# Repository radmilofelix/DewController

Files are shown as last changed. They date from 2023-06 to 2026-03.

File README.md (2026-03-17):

# DewController
 **Device to control the dew heaters and fans on astronomic instruments**
 
 Dew is an obvious nuisance for astronomic instruments and a simple way of getting rid of it are heaters placed on elements of the optical chain susceptible to forming dew.

The described device is a 6 channel heater driver, and a 2 channel fan driver, as some reflecting telescopes have a fan installed on the back of the main mirror.

The heaters and fans are driven by PWM signals software controlled by means of a STM32F103 microcontroller. The connection with the computer can be achieved either through USB or Ethernet (TCP/IP) or both.
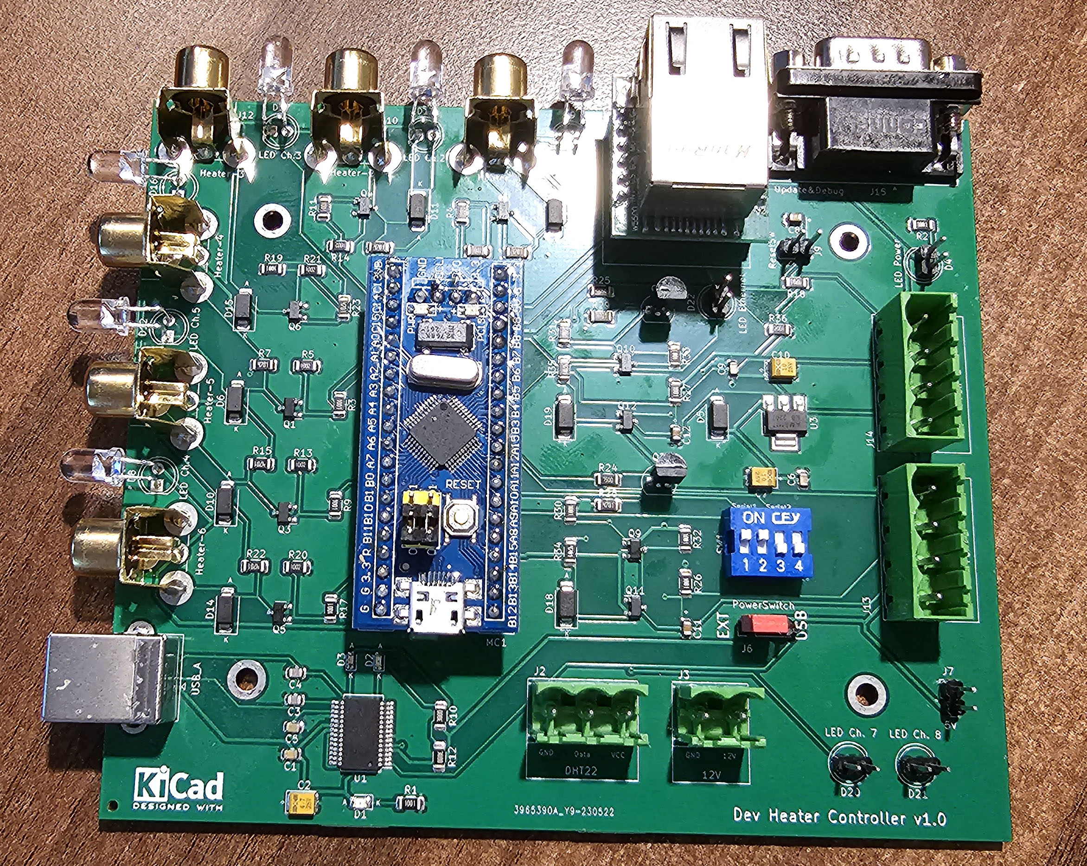
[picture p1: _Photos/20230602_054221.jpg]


The device also has a DHT22 temperature & humidity sensor, so the dew point can be computed to get an indication of whether the heaters have to be powered and how much power has to be supplied to the heaters.

# Description
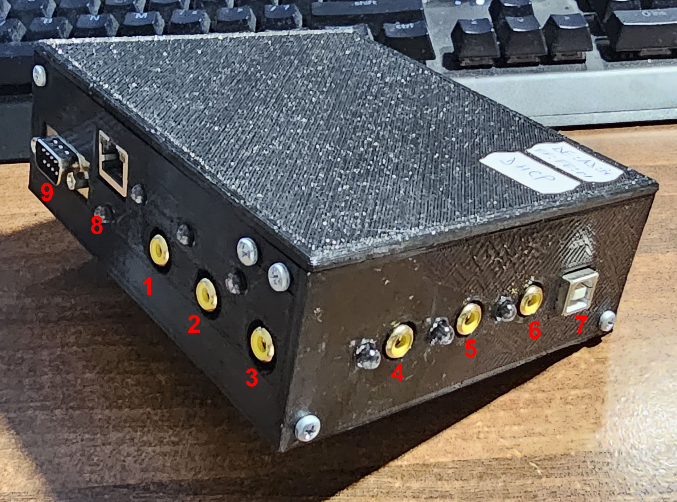
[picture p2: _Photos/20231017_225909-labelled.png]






1.  - Heater 1 (connector and LED)
2.  - Heater 2 (connector and LED)
3.  - Heater 3 (connector and LED)
4.  - Heater 4 (connector and LED)
5.  - Heater 5 (connector and LED)
6.  - Heater 6 (connector and LED)
7.  - USB connector
8.  - Ethernet Connector
9.  - Connector for servicing - 9 pin
10.  - Fan 1 (connector and LED)
11.  - Fan 2 (connector and LED)
12. - DHT 22 sensor
13. - 12V power connector
14. - Reset button
15. - Bracket for mounting the device on the telescope

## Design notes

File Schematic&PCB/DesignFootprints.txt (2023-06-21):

RCA female connectors

D-SUB 9 male connector ????

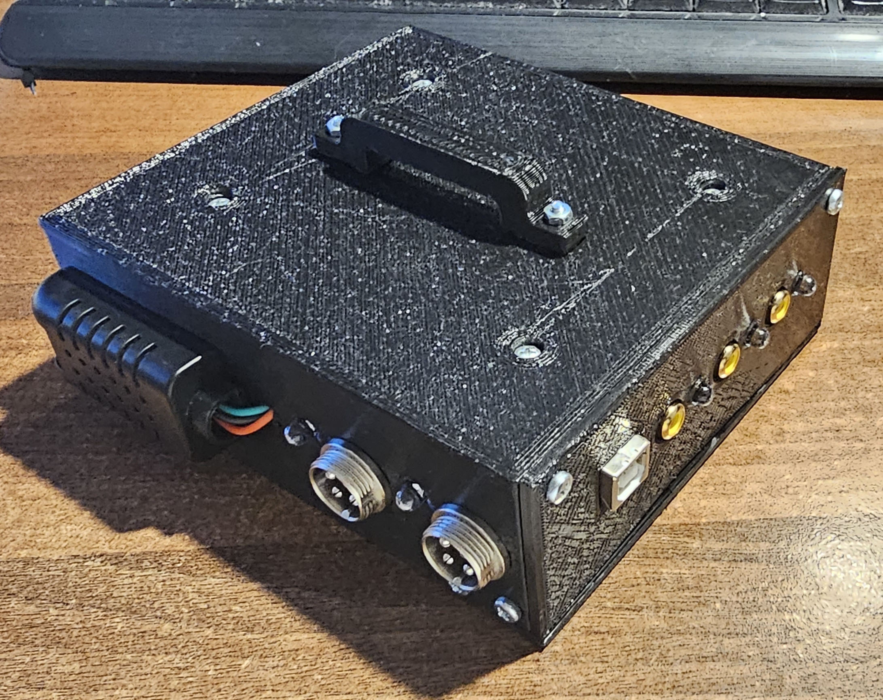
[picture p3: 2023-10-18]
_Photos/20230621_223318-labelled.jpg

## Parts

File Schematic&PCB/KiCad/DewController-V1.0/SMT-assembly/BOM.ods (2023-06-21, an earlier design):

Comment | Designator | Footprint | LCSC
100n | C1, C5, C6, C9 | Capacitor_SMD:C_0805_2012Metric | C49678
4.7u | C2 | Capacitor_Tantalum_SMD:CP_EIA-3528-21_Kemet-B | C1779
47p | C3, C4 | Capacitor_SMD:C_0805_2012Metric | C14857
10u | C7, C10 | Capacitor_Tantalum_SMD:CP_EIA-3528-21_Kemet-B | C140404
1u | C8, C11, C12 | Capacitor_SMD:C_0805_2012Metric | C28323
LED – 0805 | D1 | LED_SMD:LED_1206_3216Metric | C84256
LED Blue | D2 | LED_SMD:LED_0603_1608Metric | C72038
LED Red | D3 | LED_SMD:LED_0603_1608Metric | C72043
1N4007 | D5 | Diode_SMD:D_SMA | C22452
1N4007 | D6, D7, D10, D11, D14, D15, D18, D19 | Diode_SMD:D_SMA | C22452
IRLR3410TRPBF-SOT-23-3L-AO3400A | Q1, Q2, Q3, Q4, Q5, Q6, Q9, Q10 | Package_TO_SOT_SMD:TO-252-2 | C20917
HY19P03D-SOT23-AO3401A | Q11, Q12 | Package_TO_SOT_SMD:TO-252-2 | C15127
1k | R1 | Resistor_SMD:R_1206_3216Metric | C4410
1K | R2, R3, R4, R9, R11, R17, R19, R26, R27, R30, R31, R32, R33 | Resistor_SMD:R_1206_3216Metric | C4410
12K-10k | R5, R6, R13, R14, R20, R21 | Resistor_SMD:R_1206_3216Metric | C17902
6.8K-4.7k | R7, R8, R15, R16, R22, R23, R34, R35 | Resistor_SMD:R_1206_3216Metric | C17936
270-300 | R10, R12 | Resistor_SMD:R_1206_3216Metric | C17887
5k-4.7k | R18 | Resistor_SMD:R_1206_3216Metric | C17936
510-750 | R24, R25 | Resistor_SMD:R_1206_3216Metric | C17985
5K-4.7k | R28, R29 | Resistor_SMD:R_1206_3216Metric | C17936
3K | R36 | Resistor_SMD:R_1206_3216Metric | C17944
FT232RL | U1 | Package_SO:SSOP-28_5.3x10.2mm_P0.65mm | C8690
AZ1117-5.0 – AMS1117-5.0 | U3 | Package_TO_SOT_SMD:SOT-223 | C6187

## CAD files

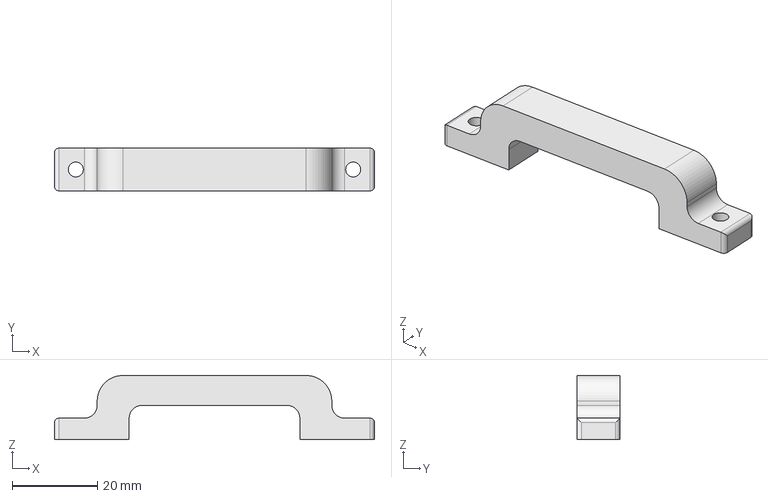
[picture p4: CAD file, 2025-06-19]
MechanicalDesigns/Case/CaseHolder.FCStd
75.0 x 10.0 x 15.0 mm

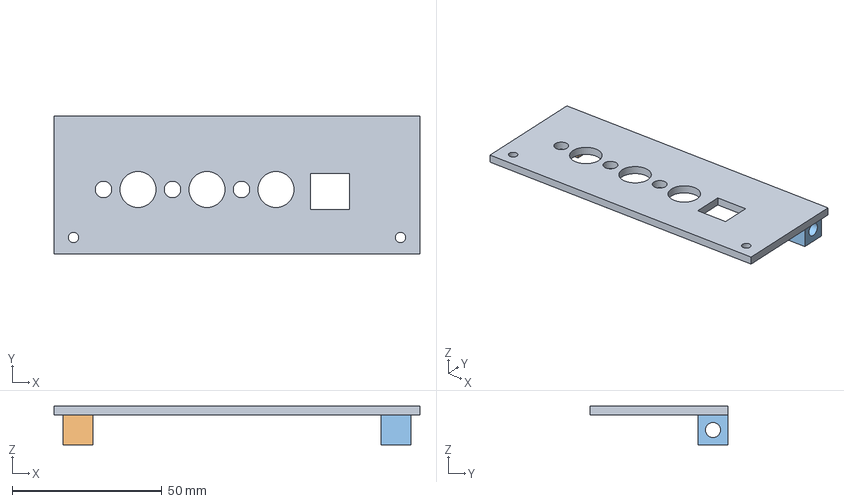
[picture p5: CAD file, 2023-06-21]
MechanicalDesigns/Case/LateralWall.FCStd
122.0 x 46.0 x 13.0 mm
M3x9_001
M3x9_002

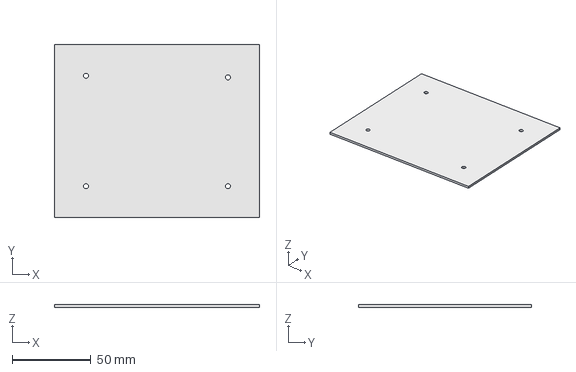
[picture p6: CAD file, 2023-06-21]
MechanicalDesigns/Case/PCB.FCStd
130.0 x 110.0 x 1.60 mm

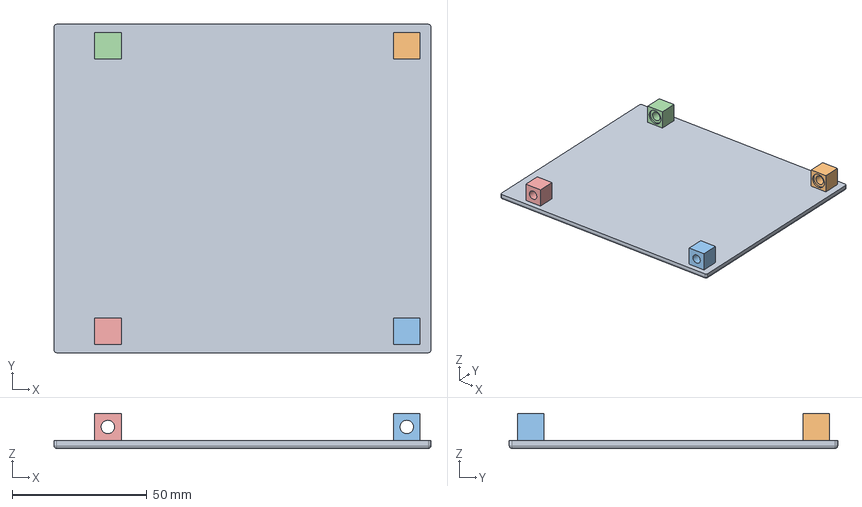
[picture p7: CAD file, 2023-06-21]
MechanicalDesigns/Case/Lid.FCStd
140.0 x 122.0 x 13.0 mm
M3x9_001
M3x9_002
M3x9_003
M3x9_004

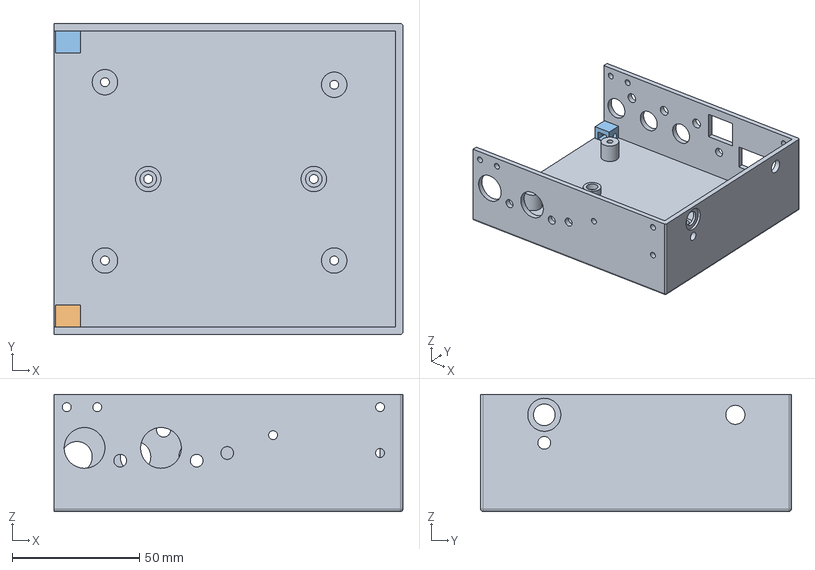
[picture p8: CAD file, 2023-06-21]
MechanicalDesigns/Case/Case.FCStd
137.0 x 122.0 x 46.0 mm
NutHolder-M3x5.7-D4.5-Knurled_Body_001
NutHolder-M3x5.7-D4.5-Knurled_001

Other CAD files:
MechanicalDesigns/Case/CaseHolder-Body.stl
MechanicalDesigns/Case/Case-Old-00.FCStd
MechanicalDesigns/Case/Case-Old-01.FCStd
MechanicalDesigns/Case/Case.stl
MechanicalDesigns/Case/LateralWall.stl
MechanicalDesigns/Case/Lid.stl

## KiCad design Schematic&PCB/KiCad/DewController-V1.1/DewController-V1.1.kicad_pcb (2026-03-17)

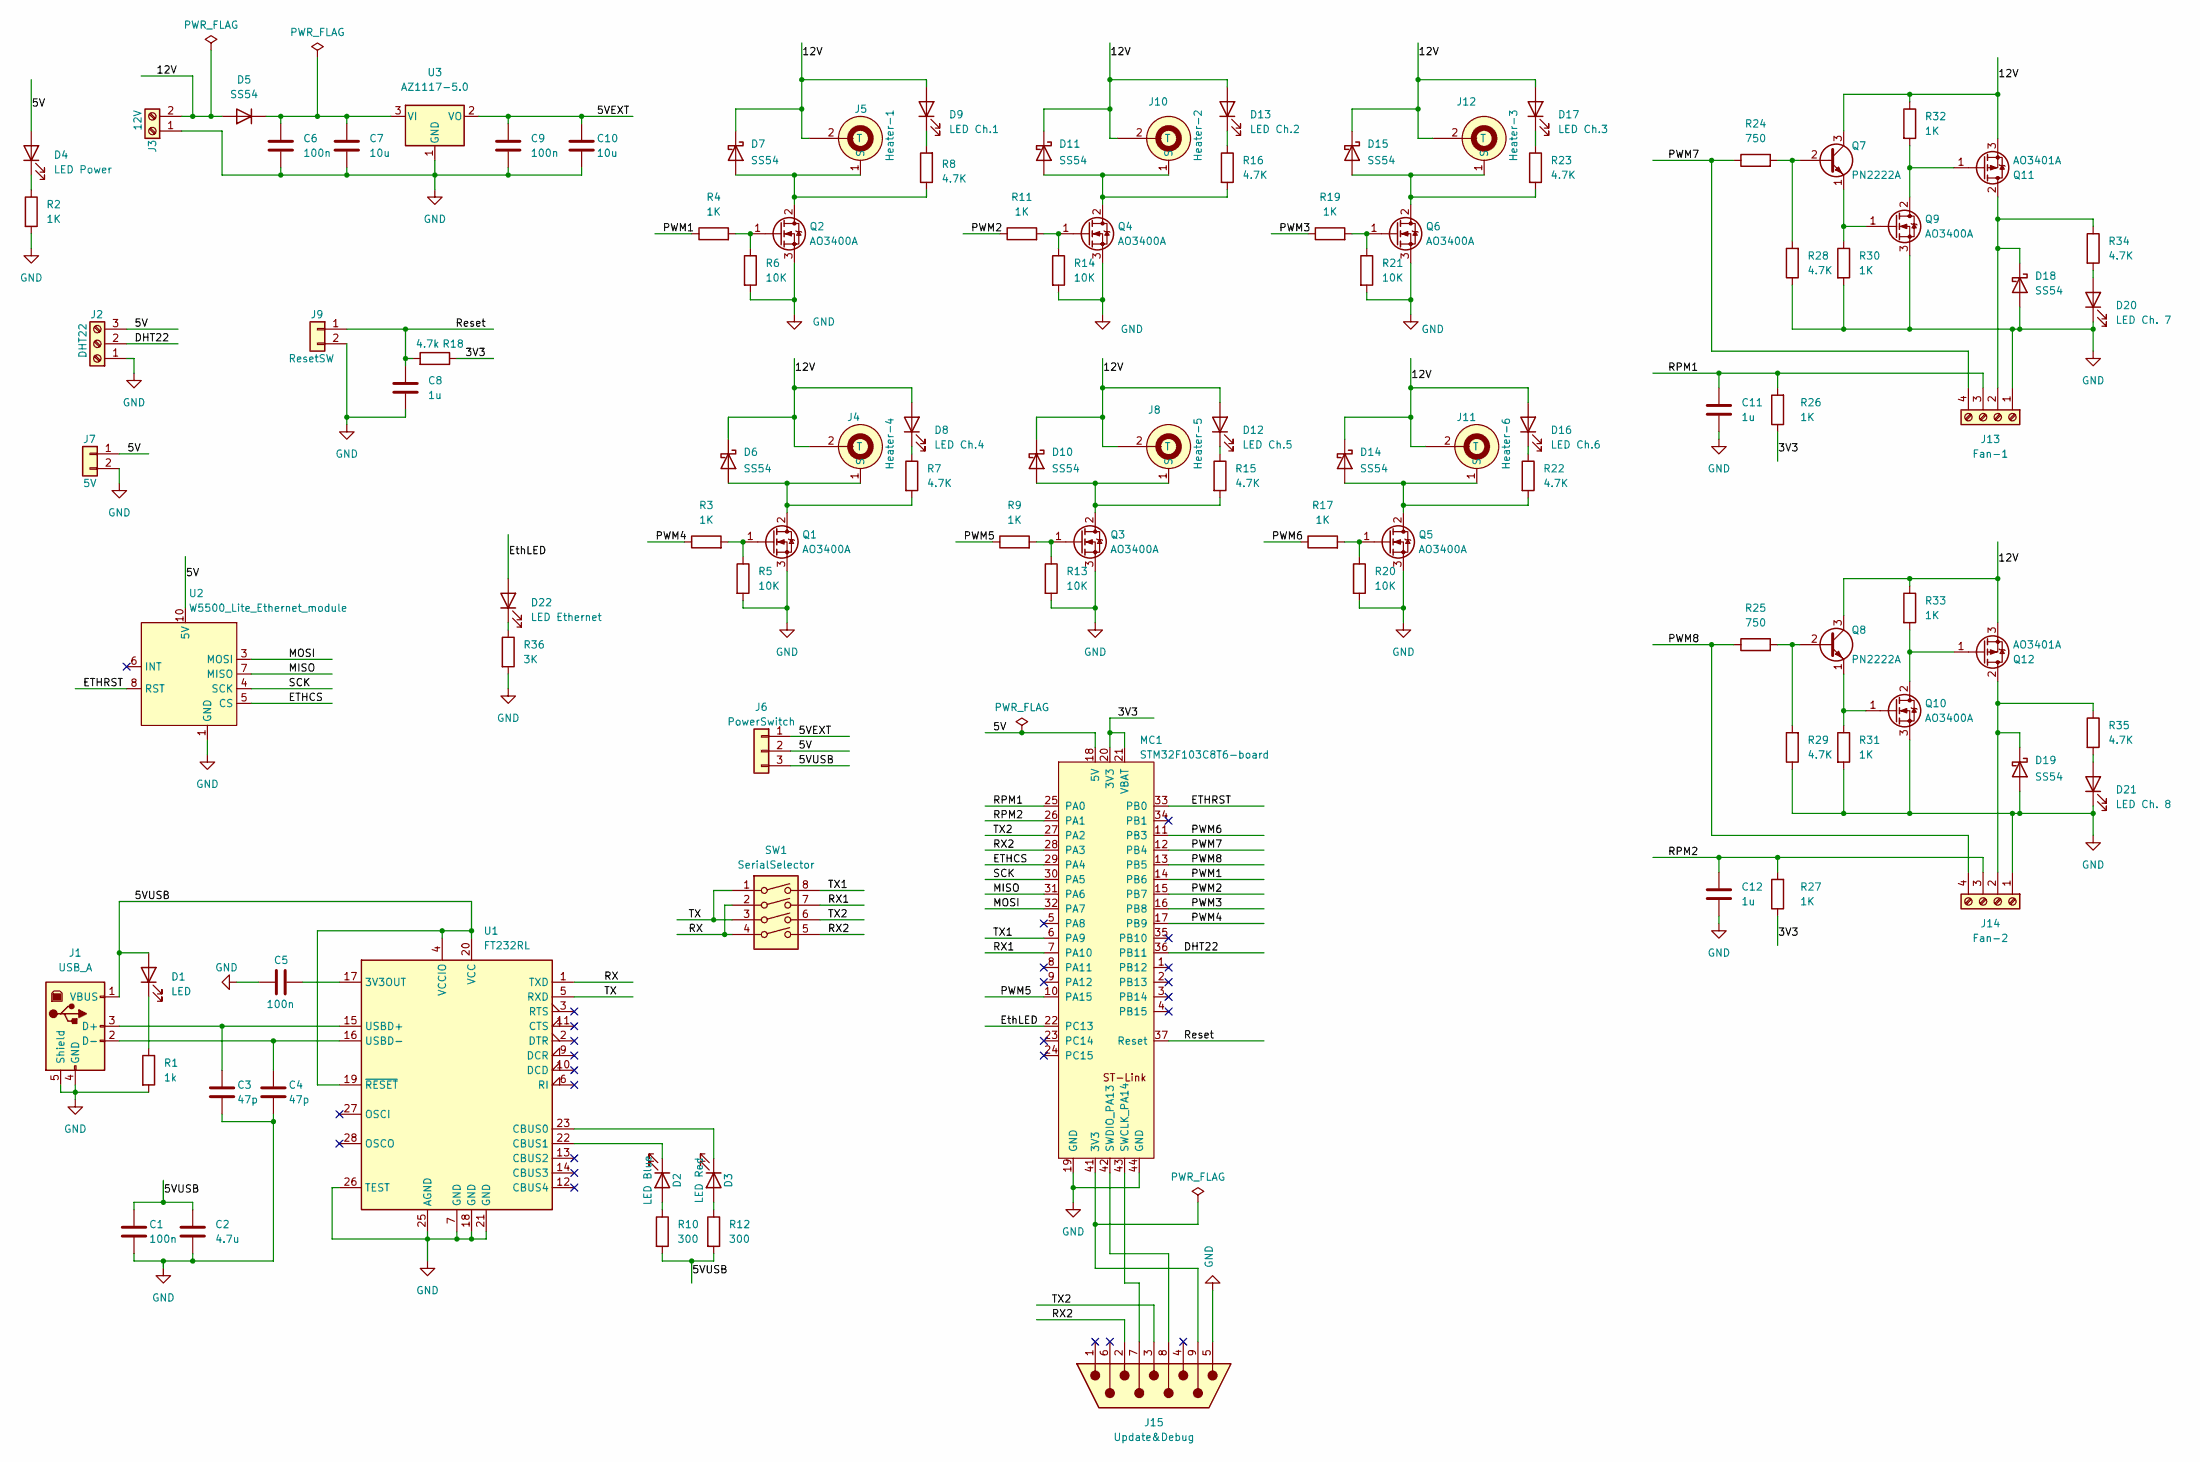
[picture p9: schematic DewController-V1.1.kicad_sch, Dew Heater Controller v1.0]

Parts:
C1, C5, C6, C9: 100n; C_0805_2012Metric; LCSC C49678
C2: 4.7u; CP_EIA-3528-21_Kemet-B; LCSC C1779
C3, C4: 47p; C_0805_2012Metric; LCSC C14857
C7, C10: 10u; CP_EIA-3528-21_Kemet-B; LCSC C140404
C8, C11, C12: 1u; C_0805_2012Metric; LCSC C28323
D1: LED; LED_0805_2012Metric; LCSC C84256
D2: LED Blue; LED_0603_1608Metric; LCSC C72038
D3: LED Red; LED_0603_1608Metric; LCSC C72043
D4: LED Power; LED_D5.0mm
D5, D6, D7, D10, D11, D14, D15, D18, D19: SS54; D_SMA; LCSC C22452
D8: LED Ch.4; LED_D5.0mm
D9: LED Ch.1; LED_D5.0mm
D12: LED Ch.5; LED_D5.0mm
D13: LED Ch.2; LED_D5.0mm
D16: LED Ch.6; LED_D5.0mm
D17: LED Ch.3; LED_D5.0mm
D20: LED Ch. 7; LED_D5.0mm
D21: LED Ch. 8; LED_D5.0mm
D22: LED Ethernet; LED_D5.0mm
J1: USB_A; USB_B_Lumberg_2411_02_Horizontal
J2: DHT22; TerminalBlock_PTR_AKZ950-3_P5.08mm_Vertical
J3: 12V; TerminalBlock_PTR_AKZ950-2_P5.08mm_Vertical
J4: Heater-4; RCA_F_4Pin_15mm_11mm
J5: Heater-1; RCA_F_4Pin_15mm_11mm
J6: PowerSwitch; PinHeader_1x03_P2.54mm_Vertical
J7: 5V; PinHeader_1x02_P2.54mm_Vertical
J8: Heater-5; RCA_F_4Pin_15mm_11mm
J9: ResetSW; PinHeader_1x02_P2.54mm_Vertical
J10: Heater-2; RCA_F_4Pin_15mm_11mm
J11: Heater-6; RCA_F_4Pin_15mm_11mm
J12: Heater-3; RCA_F_4Pin_15mm_11mm
J13: Fan-1; TerminalBlock_PTR_AKZ950-4_P5.08mm_Vertical
J14: Fan-2; TerminalBlock_PTR_AKZ950-4_P5.08mm_Vertical
J15: Update&Debug; DSUB-9_Male_Horizontal_P2.77x2.84mm_EdgePinOffset4.94mm_Hou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
MC1: STM32F103C8T6-board; STM32F103C8T6
Q1, Q2, Q3, Q4, Q5, Q6, Q9, Q10: AO3400A; SOT-23-3-DS-inv; LCSC C20917
Q7, Q8: PN2222A; TO-92_Inline
Q11, Q12: AO3401A; SOT-23-DS-inv; LCSC C15127
R1: 1k; R_1206_3216Metric; LCSC C4410
R2, R3, R4, R9, R11, R17, R19, R26, R27, R30, R31, R32, R33: 1K; R_1206_3216Metric; LCSC C4410
R5, R6, R13, R14, R20, R21: 10K; R_1206_3216Metric; LCSC C17902
R7, R8, R15, R16, R22, R23, R28, R29, R34, R35: 4.7K; R_1206_3216Metric; LCSC C17936
R10, R12: 300; R_1206_3216Metric; LCSC C17887
R18: 4.7k; R_1206_3216Metric; LCSC C17936
R24, R25: 750; R_1206_3216Metric; LCSC C17985
R36: 3K; R_1206_3216Metric; LCSC C17944
SW1: SerialSelector; DIP-8_W7.62mm
U1: FT232RL; SSOP-28_5.3x10.2mm_P0.65mm; LCSC C8690
U2: W5500_Lite_Ethernet_module; W5500_Lite
U3: AZ1117-5.0; SOT-223; LCSC C6187

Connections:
/3V3: MC1.20 (3V3), MC1.21 (VBAT), MC1.38 (3V3), R18.1, R26.1, R27.1
/5V: D4.2 (A), J2.3, J6.2, J7.1, MC1.18 (5V), U2.10 (5V), U2.11 (5V)
/5VEXT: C9.1, C10.1, J6.1, U3.2 (VO)
/5VUSB: C1.1, C2.1, D1.2 (A), J1.1 (VBUS), J6.3, R10.2, R12.2, U1.4 (VCCIO), U1.19 (~RESET), U1.20 (VCC)
/12V: D5.2 (A), D6.1 (K), D7.1 (K), D8.2 (A), D9.2 (A), D10.1 (K), D11.1 (K), D12.2 (A), D13.2 (A), D14.1 (K), D15.1 (K), D16.2 (A), D17.2 (A), J3.2, J4.2 (T), J5.2 (T), J8.2 (T), J10.2 (T), J11.2 (T), J12.2 (T), Q7.3 (C), Q8.3 (C), Q11.3 (S), Q12.3 (S), R32.1, R33.1
/DHT22: J2.2, MC1.36 (PB11)
/ETHCS: MC1.29 (PA4), U2.5 (CS)
/ETHRST: MC1.33 (PB0), U2.8 (RST)
/EthLED: D22.2 (A), MC1.22 (PC13)
/MISO: MC1.31 (PA6), U2.7 (MISO)
/MOSI: MC1.32 (PA7), U2.3 (MOSI)
/PWM1: MC1.14 (PB6), R4.1
/PWM2: MC1.15 (PB7), R11.1
/PWM3: MC1.16 (PB8), R19.1
/PWM4: MC1.17 (PB9), R3.1
/PWM5: MC1.10 (PA15), R9.1
/PWM6: MC1.11 (PB3), R17.1
/PWM7: J13.4, MC1.12 (PB4), R24.1
/PWM8: J14.4, MC1.13 (PB5), R25.1
/RPM1: C11.1, J13.3, MC1.25 (PA0), R26.2
/RPM2: C12.1, J14.3, MC1.26 (PA1), R27.2
/RX: SW1.2, SW1.4, U1.1 (TXD)
/RX1: MC1.7 (PA10), SW1.7
/RX2: J15.2, MC1.28 (PA3), SW1.5
/Reset: C8.1, J9.1, MC1.37 (Reset), R18.2
/SCK: MC1.30 (PA5), U2.4 (SCK)
/TX: SW1.1, SW1.3, U1.5 (RXD)
/TX1: MC1.6 (PA9), SW1.8
/TX2: J15.3, MC1.27 (PA2), SW1.6
GND: C1.2, C2.2, C3.2, C4.2, C5.2, C6.2, C7.2, C8.2, C9.2, C10.2, C11.2, C12.2, D18.2 (A), D19.2 (A), D20.1 (K), D21.1 (K), J1.4 (GND), J1.5 (Shield), J2.1, J3.1, J7.2, J9.2, J13.1, J14.1, J15.5, MC1.19 (GND), MC1.39 (GND), MC1.40 (GND), MC1.44 (GND), Q1.3 (S), Q2.3 (S), Q3.3 (S), Q4.3 (S), Q5.3 (S), Q6.3 (S), Q9.3 (S), Q10.3 (S), R1.2, R2.2, R5.2, R6.2, R13.2, R14.2, R20.2, R21.2, R28.1, R29.1, R30.2, R31.2, R36.2, U1.7 (GND), U1.18 (GND), U1.21 (GND), U1.25 (AGND), U1.26 (TEST), U2.1 (GND), U2.2 (GND), U2.12 (GND), U3.1 (GND)
unnamed: D1.1 (K), R1.1
unnamed: D2.2 (A), R10.1
unnamed: D2.1 (K), U1.22 (CBUS1)
unnamed: D3.2 (A), R12.1
unnamed: D3.1 (K), U1.23 (CBUS0)
unnamed: D4.1 (K), R2.1
unnamed: C6.1, C7.1, D5.1 (K), U3.3 (VI)
unnamed: D6.2 (A), J4.1 (S), J4.3 (S), J4.4 (S), Q1.2 (D), R7.2
unnamed: D7.2 (A), J5.1 (S), J5.3 (S), J5.4 (S), Q2.2 (D), R8.1
unnamed: D8.1 (K), R7.1
unnamed: D9.1 (K), R8.2
unnamed: D10.2 (A), J8.1 (S), J8.3 (S), J8.4 (S), Q3.2 (D), R15.2
unnamed: D11.2 (A), J10.1 (S), J10.3 (S), J10.4 (S), Q4.2 (D), R16.2
unnamed: D12.1 (K), R15.1
unnamed: D13.1 (K), R16.1
unnamed: D14.2 (A), J11.1 (S), J11.3 (S), J11.4 (S), Q5.2 (D), R22.2
unnamed: D15.2 (A), J12.1 (S), J12.3 (S), J12.4 (S), Q6.2 (D), R23.2
unnamed: D16.1 (K), R22.1
unnamed: D17.1 (K), R23.1
unnamed: D18.1 (K), J13.2, Q11.2 (D), R34.1
unnamed: D19.1 (K), J14.2, Q12.2 (D), R35.1
unnamed: D20.2 (A), R34.2
unnamed: D21.2 (A), R35.2
unnamed: D22.1 (K), R36.1
unnamed: C3.1, J1.3 (D+), U1.15 (USBD+)
unnamed: C4.1, J1.2 (D-), U1.16 (USBD-)
unnamed: J15.9, MC1.41 (3V3)
unnamed: J15.7, MC1.43 (SWCLK_PA14)
unnamed: J15.8, MC1.42 (SWDIO_PA13)
unnamed: Q1.1 (G), R3.2, R5.1
unnamed: Q2.1 (G), R4.2, R6.1
unnamed: Q3.1 (G), R9.2, R13.1
unnamed: Q4.1 (G), R11.2, R14.1
unnamed: Q5.1 (G), R17.2, R20.1
unnamed: Q6.1 (G), R19.2, R21.1
unnamed: Q7.2 (B), R24.2, R28.2
unnamed: Q7.1 (E), Q9.1 (G), R30.1
unnamed: Q8.2 (B), R25.2, R29.2
unnamed: Q10.2 (D), Q12.1 (G), R33.2
unnamed: Q8.1 (E), Q10.1 (G), R31.1
unnamed: Q9.2 (D), Q11.1 (G), R32.2
unnamed: C5.1, U1.17 (3V3OUT)

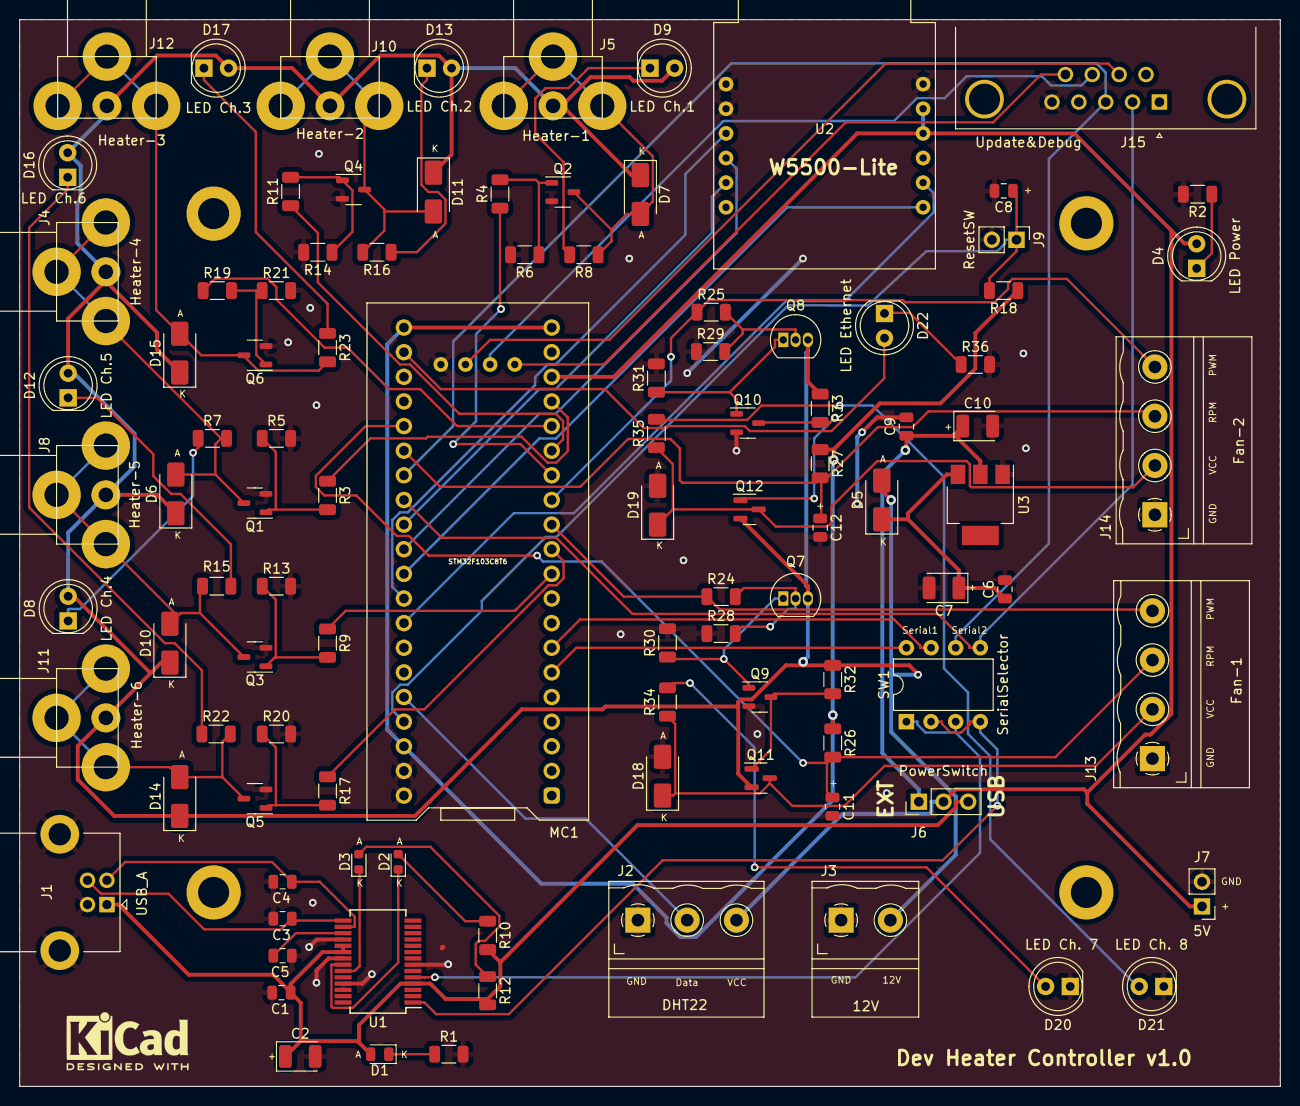
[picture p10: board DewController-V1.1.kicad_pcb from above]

Board: 2 copper layers, 130.0 x 110.0 mm, 106 parts (0 on the bottom side), 72 nets.

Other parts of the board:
MH1, MH2, MH3, MH4: MountingHole_3.2mm_M3_DIN965_Pad

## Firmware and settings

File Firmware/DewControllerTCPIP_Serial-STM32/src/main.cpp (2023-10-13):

/*
Dew heater controller serving 2 TCP clients and a Serial client on Serial2

To have only one TCP client, eliminate the following variables and the corresponding code:
EthernetClient client1;
int dewHeaterDriverConnect1 = 0;
unsigned long dewDriverTimer1;
bool isTCPalreadyConnected1 = false;
bool isTCPrequest1 = false;

STM32F103C8T6
MISO - A6
MOSI - A7
CLK -  A5
CS -   A4
W5500 reset - B0

It is recommended to power the W5500 with 5V.
The SPI lines will work at 3.3V for high logic level.

If W5500 is powered at 3.3V, might will still work but the
MISO line will drop to 2V for high logic level which is the low limit for it.
Variations in 3.3 power supply may render the W5500 unresponsive.

Pull the reset pin of W5500 up to Vcc with a 5Kohm resistor. Use a 5V tolerant
pin of the STM32 module to reset the W5500 at startup.
*/


#include "dewHeaterController.h"

#define RPMPIN1 PA0
#define RPMPIN2 PA1
#define MAGPOLES 2 // number of poles driving the Hall sensor
#define ETHLED PC13

#define DHTPIN PB11
#define DHTTYPE DHT22 // DHT 22  (AM2302), AM2321
long rpm = 0;
int speed = 9999;
DHT dhtSensor(DHTPIN,DHTTYPE);


void setup()
{
    dhtSensor.begin();
    pwmPin[0] = PB6;
    pwmPin[1] = PB7;
    pwmPin[2] = PB8;
    pwmPin[3] = PB3;
    pwmPin[4] = PA15;
    pwmPin[5] = PB9;
    pwmPin[6] = PB4;
    pwmPin[7] = PB5;

    analogWriteFrequency(25000); // set PWM frequency - all timers - to 25KHz (default is 1kHz)
//  analogWriteFrequency(8000); // set PWM frequency - all timers - to 8KHz (default is 1kHz)
//  analogWriteFrequency(1000); // set PWM frequency - all timers - to 1KHz - default
//  analogWriteResolution(ANALOGWRITERESOLUTION); // default

    for(int i=0; i<8; i++)
    {
        pinMode(pwmPin[i], OUTPUT);
        analogWrite(pwmPin[i],0);
    }

// Reset W5500 before starting
    pinMode(RESETPIN, OUTPUT);
    digitalWrite(RESETPIN, LOW);
    delay(300);
    digitalWrite(RESETPIN, HIGH);
    delay(300);

//  switch off ETH LED
    pinMode(ETHLED, OUTPUT);
    digitalWrite(ETHLED, LOW);

  // Open serial communications and wait for port to open:
//  Serial2.begin(19200);  // PA3  (RX)  PA2  (TX)
    Serial.begin(115200);  // PA10  (RX)  PA9  (TX)
    Serial.setTimeout(500);
//  Serial.setTimeout(3000);
#ifdef DEBUG
    Serial.println(""); Serial.println(""); Serial.println(""); Serial.println("");
    Serial.println("Serial1 started...");
#endif

//    initialize the Ethernet device
    #ifdef DHCP
        Ethernet.begin(mac); // DHCP
    #else
        Ethernet.begin(mac, ip);
    #endif

  // Check for Ethernet hardware present
    if (Ethernet.hardwareStatus() == EthernetNoHardware)
    {
        digitalWrite(ETHLED, LOW);
#ifdef DEBUG
        Serial.println("Ethernet shield was not found.  Sorry, can't connect to ethernet without hardware.");
#endif
    }
    else
    {
        digitalWrite(ETHLED, HIGH);
    }
    delay(2000);
    if (Ethernet.linkStatus() == LinkOFF)
    {
        digitalWrite(ETHLED, LOW);
#ifdef DEBUG
        Serial.println("Ethernet cable is not connected.");
#endif
    }
    else
    {
        digitalWrite(ETHLED, HIGH);
    }

  // start listening for clients
//  server.begin();

#ifdef DEBUG
    Serial.print("Dew controller IP address: ");
    Serial.println(Ethernet.localIP());
#endif

    dewControllerData.command = 0;
    dewControllerData.fanRPMcapability = 0;
    dewControllerData.temperature = 0;
    dewControllerData.airHumidity = 0;
    dewControllerData.airPressure = 0;
    for (int i = 0; i < 8; i++)
    {
        dewControllerData.pwmDevice[i] = 0;
    }
} // setup()


long GetRPM(int fanNumber)
{
  long localRPM;
  switch(fanNumber)
  {
      case 1:
        if(dewControllerData.fanRPMcapability & 1)
        {
            localRPM = pulseInLong(RPMPIN1, HIGH)* MAGPOLES * 2; // duration of one rotation of the fan (us)//
        }
        else
        {
            localRPM = 0;
        }
      break;
      
      case 2:
        if(dewControllerData.fanRPMcapability & 2)
        {
            localRPM = pulseInLong(RPMPIN2, HIGH)* MAGPOLES * 2; // duration of one rotation of the fan (us)//
        }
        else
        {
            localRPM = 0;
        }
      break;
      
      default:
      localRPM = 0;
  }
  if(localRPM > 0)
  {
    localRPM = 60000000 / localRPM;
  }
  return localRPM;
}


long GetDebouncedRPM(int fanNumber)
{
  switch(fanNumber)
  {
    case 1:
        if(dewControllerData.pwmDevice[6] < 1 || !(dewControllerData.fanRPMcapability & 1 ))
        {
            return 0;
        }
    break;

    case 2:
        if(dewControllerData.pwmDevice[7] < 1 || !(dewControllerData.fanRPMcapability & 2 ))
        {
            return 0;
        }
    break;
  }
  long localRPM;
  for(int i=0; i<20; i++)
  {

    localRPM = GetRPM(fanNumber);
    long diff = abs(rpm - localRPM);
    if(diff < 100 && localRPM < 2000)
    {
        rpm = localRPM;
        return rpm;
    }
  }
  if(localRPM > 2500)
  {
    rpm = 0;
  }
  else
  {
    rpm = localRPM;
  }
  return rpm;
}


void PackData()
{
    PollDhtSensor();
    char dataElement[100];
    buffer[0] = 0;
    itoa( dewControllerData.command, dataElement, 10);
    strcat(buffer, dataElement);
    strcat(buffer, ",");
    for (int i = 1; i < 9; i++)
    {
        itoa( dewControllerData.pwmDevice[i-1], dataElement, 10);
        strcat(buffer, dataElement);
        strcat(buffer, ",");
    }
        for (int i = 9; i < 15; i++)
    {
        switch (i)
        {
        case 9:
            itoa( dewControllerData.fanRPMcapability, dataElement, 10);
            break;
        case 10:
            itoa( dewControllerData.temperature, dataElement, 10);
            break;
        case 11:
            itoa( dewControllerData.airHumidity, dataElement, 10);
            break;
        case 12:
            itoa( dewControllerData.airPressure, dataElement, 10);
            break;
        case 13:
            itoa( dewControllerData.rpm1, dataElement, 10);
            break;
        case 14:
            itoa( dewControllerData.rpm2, dataElement, 10);
            break;
        default:
            break;
        }
        strcat(buffer, dataElement);
        strcat(buffer, ",");
    }
    int i = strlen(buffer);
    buffer[i-1] = 0;
}


void UnpackData(char* dataString)
{
    char localString[100];
    int charCounter = 0;
    int dataCounter = 0;
    int d = strlen(dataString);
    for (int i = 0; i < d; i++)
    {
        if(dataString[i] != ',')
        {
            localString[charCounter] = dataString[i];
            charCounter++;
        }
        else
        {
            localString[charCounter] = 0;
            charCounter = 0;
            switch (dataCounter)
            {
            case 0:
                dewControllerData.command = atoi(localString);
                break;
            case 1: case 2: case 3: case 4: case 5: case 6: case 7: case 8:
                dewControllerData.pwmDevice[dataCounter-1] = atoi(localString);
                break;
            case 9:
                dewControllerData.fanRPMcapability = atoi(localString);
                break;
            default:
                break;
            }
            dataCounter++;
        }

    }
}


void SetHeatersAndFans()
{
    for(int i=0; i<8; i++)
    {
        analogWrite(pwmPin[i], dewControllerData.pwmDevice[i]);
    }
}


//*
#ifdef DEBUG
void DisplayData()
{
    PollDhtSensor();

    Serial.print("Command: "); Serial.println(dewControllerData.command);
    for (int i = 0; i < 8; i++)
    {
        Serial.print("pwmDevice ");
        Serial.print(i);
        Serial.print(": ");
        Serial.println(dewControllerData.pwmDevice[i]);
    }

    Serial.println();
    Serial.print("temperature: "); Serial.println(dewControllerData.temperature/100);
    Serial.print("airHumidity: "); Serial.println(dewControllerData.airHumidity/100);
    Serial.println();
    Serial.print("airPressure: "); Serial.println(dewControllerData.airPressure);
    Serial.println();

    Serial.print("Fans RPM capability: "); Serial.println(dewControllerData.fanRPMcapability);
    Serial.println();

    Serial.print("RPM 1: "); Serial.println(dewControllerData.rpm1);
    Serial.print("RPM 2: "); Serial.println(dewControllerData.rpm2);
    Serial.println();


}
#endif
//*/


void PollDhtSensor()
{
    dewControllerData.temperature = dhtSensor.readTemperature()*100;
    dewControllerData.airHumidity = dhtSensor.readHumidity()*100;
}


void HartBeat()
{
    char txBuffer[50];
    strcpy(txBuffer, HARTBEATRESPONSE);

    if(serialservices.isSerialRequest)
    {
        serialservices.SendResponse(txBuffer);
    }

    if(tcpservice.isTCPrequest)
    {
        tcpservice.clientTimer = millis();
        tcpservice.clientConnect = 1;
        tcpservice.SendResponse(txBuffer);
    }
    if(tcpservice1.isTCPrequest)
    {
        tcpservice1.clientTimer = millis();
        tcpservice1.clientConnect = 1;
        tcpservice1.SendResponse(txBuffer);
    }
}


void SelectAndSend(char *response)
{
    if(serialservices.isSerialRequest)
    {
        serialservices.SendResponse(response);
    }
    if(tcpservice.isTCPrequest)
    {
        tcpservice.SendResponse(response);
    }
    if(tcpservice1.isTCPrequest)
    {
        tcpservice1.SendResponse(response);
    }
    buffer[0] = 0;
}


void ProcessRequests()
{
#ifdef DEBUG
    if(strlen(buffer))
    {
//      Serial.print("\r\nReceived: ");
//      Serial.println(buffer);
    }
#endif

    if(!strcmp(buffer,HARTBEATCALL))
    {
        HartBeat();
        return;
    }

    if(!strcmp(buffer,GETDATA))
    {
        dewControllerData.command = GETDATAHEADER;
        PackData();
        SelectAndSend(buffer);
        return;
    }

    if(!strcmp(buffer,GETRPM))
    {
        dewControllerData.rpm1 = GetDebouncedRPM(1);
        dewControllerData.rpm2 = GetDebouncedRPM(2);
        SelectAndSend((char*)CONFIRMATION);
    }
    
    if ( !strncmp(buffer, SETDATA, 4) )
//  if (buffer[0] == '2' && buffer[1] == '8' && buffer[2] == '1'&& buffer[3] == '3' && buffer[4] == ',')
                      //UnpackData("2735,11,22,33,44,55,66,111,222,11,853,9025,51,52,53,54,55,56,57,58");
                      // Serial.println(GetDebouncedRPM(), DEC);

                      // 2735,0,0,0,0,0,0,0,0,0,
                      // 2735,2,2,2,2,2,2,2,2,0,
                      // 2735,4,4,4,4,4,4,4,4,0,
                      // 2735,8,8,8,8,8,8,8,8,0,
                      // 2735,16,16,16,16,16,16,16,16,0
                      // 2735,32,32,32,32,32,32,32,32,0
                      // 2735,64,64,64,64,64,64,64,64,0,
                      // 2735,127,127,127,127,127,127,127,127,0,
                      // 2735,255,255,255,255,255,255,255,255,0,


    {
        UnpackData(buffer);
        SetHeatersAndFans();
        SelectAndSend((char*)CONFIRMATION);
        #ifdef DEBUG
        DisplayData();
        #endif
        return;
    }
    buffer[0] = 0;
}


void loop()
{
    tcpservice.CheckTCPClient(buffer);
    tcpservice1.CheckTCPClient(buffer);
    serialservices.CheckSerialClient(buffer);
    ProcessRequests();
    tcpservice.CheckConnections();
    tcpservice1.CheckConnections();
}

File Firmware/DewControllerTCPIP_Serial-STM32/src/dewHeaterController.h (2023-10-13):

#ifndef DEWHEATERCONTROLLER__H
#define DEWHEATERCONTROLLER__H

#include <cstdio>
#include <stdlib.h>
#include <string.h>   //strlen  
#include <errno.h>  
#include <unistd.h>   //close  
#include <sys/stat.h>
#include <sys/Time.h>
#include <chrono>
#include <OneWire.h>
#include <DallasTemperature.h>
#include <DHT.h> 
#include <Adafruit_BME280.h>

#include <SPI.h>
#include <Ethernet.h>

#include "TCPServices.h"
#include "SerialServices.h"

//#define DEBUG

#define DHCP
#define TCPPORT 20002
#define TCPPORT1 20003
#define ANALOGWRITERESOLUTION 8 // default

#define RESETPIN PB0

#define HARTBEATCALL "YOOHOO"
#define HARTBEATRESPONSE "2u2"
#define GETDATA "gd"
#define GETDATAHEADER 11
#define SETDATA "2813,"
#define CONFIRMATION "OK"
#define GETRPM "grpm"

// Enter a MAC address and IP address for your controller below.
// The IP address will be dependent on your local network.
// gateway and subnet are optional:
byte mac[] =
{
  0xDE, 0xAD, 0xBE, 0xEF, 0xFE, 0x01 // black DHT
//  0xDE, 0xAD, 0xBE, 0xEF, 0xFE, 0x02 // white DHT
};

#ifndef DHCP
    IPAddress ip(192, 168, 111, 176); // black DHT
//    IPAddress ip(192, 168, 111, 177); // white DHT

//    IPAddress myDns(192, 168, 111, 1);
//    IPAddress gateway(192, 168, 111, 1);
//    IPAddress subnet(255, 255, 255, 0);
#endif

struct DEWCONTROLLERDATA
{   
	int command;
	int pwmDevice[8];
	int fanRPMcapability; // bit0 = 1 Fan1 has rpm capability; bit1 = 1 -> Fan2 has rpm capability 
	int temperature;
	int airHumidity;
	int airPressure;
	long rpm1;
	long rpm2;
} dewControllerData;

int pwmPin[32];

// Initialise the second serial port on STM32
HardwareSerial Serial2(USART2);   // PA3  (RX)  PA2  (TX)

TCPServices tcpservice(TCPPORT);
TCPServices tcpservice1(TCPPORT1);
SerialServices serialservices;


int dewHeaterDriverConnect = 0; 
int dewHeaterDriverConnect1 = 0;
unsigned long dewDriverTimer;
unsigned long dewDriverTimer1;
bool isTCPalreadyConnected = false;
bool isTCPalreadyConnected1 = false;
bool isTCPrequest = false;
bool isTCPrequest1 = false;
bool isSerialrequest = false;
char buffer[1025];  // 1k communication buffer

void setup();
void ReportDewHeaterDriverConnect();
void ProcessRequests();
void SetHeatersAndFans();
void SelectAndSend(char *response);
int main ( int argument, char const *argv[] );
void PollDhtSensor();
long GetRPM(int fanNumber);
long GetDebouncedRPM(int fanNumber);
void HartBeat();

#endif

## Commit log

2023-07-15 current work
2023-08-19 Unique MAC addresses to devices
2023-10-13 finished the INDI driver
2024-02-08 Correct heaters numbers
2024-06-15 updated INDI driver to indilib 2.8.0
    [DewController-V1.1.kicad_sch]
2025-06-19 Code was adapted for the new INDI library v2.1.4, CMakeLists.txt optimised
    [CaseHolder.FCStd, DewController-V1.1.kicad_sch]
2026-03-17 Location update
    [DewController-V1.1.kicad_pcb, DewController-V1.1.kicad_sch]
